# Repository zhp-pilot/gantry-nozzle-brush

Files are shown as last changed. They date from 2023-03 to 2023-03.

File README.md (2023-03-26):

# Gantry mounted nozzle brush for V2 and Trident TAP users.

Gantry Nozzle Scrubber_small

## CREDITS

This is an adaptation of the Decontaminator Nozzle Scrubber by [edwardyeeks]( https://mods.vorondesign.com/detail/eiGz71BOprk2GapXbQVgA). The mount is derived from the fixed Klicky mount by [jlas1]( https://github.com/jlas1/Klicky-Probe).

## DISCLAIMER 

***THIS MOD IS INTENDED FOR ADVANCED USERS ONLY AND WILL REQUIRE SETTING UP YOUR PRINTER WITH VERY TIGHT TOLERANCES, LIKELY REQUIRING MODIFYING YOUR Y-MAX AND ADJUSTING YOUR PHYSICAL BED LOCATION IF YOU WANT TO RETAIN THE FULL XY BUILD AREA OF YOUR PRINTER. READ THIS WRITE UP AND THE PROVIDED CONFIG FILE IN THEIR ENTIRITY BEFORE PROCEEDING. YOU ARE USING THIS MOD AT YOU OWN RISK AND THE AUTHOR ASSUMES NO LIABILTY FOR ANY DAMAGE RESULTING FROM ITS USE.***

## PURPOSE
This mod is intended for users of TAP to provide a safe nozzle cleaning routine that can be performed at the end of the print. With the original Nozzle Scrubber mod, the Z has to lower to the brush, risking crashing the toolhead into printed parts if performed at the end of a print. With this mod, the scrubbing can be performed at any height as the brush is mounted to the gantry. There are no Z movements in the provided config, as such, the cleaning will be performed at the current height when the macro is called.

**This mod is NOT recommended for Klicky, Euclid, or any variant that has a probe dock mounted on the rear gantry extrusion.** The intent is for this mount to be installed where the probe mount would typically be installed on the far left. Trying to use this mod in conjunction with another gantry-mounted mod, one risks the movements of the two interfering with each other and potentially causing damage. There are NO safety parameters in the macro to check if the movements are safe and won't collide with other objects.

## IMPORTANT INFO
On a 2.4, the gantry mount needs to be installed so that it clears the bed extrusions. On a standard bed install, the mount will hit the extrusion during homing, QGL, and bed mesh operations, and maybe even when the nozzle is at 1-2 mm or below. Remember with TAP, the gantry actually keeps moving down after the nozzle hits the bed.  I don’t have a Trident to test on, but I assume the same would hold true for the rear bed mount extrusion.

The standard gantry mount has an overall height of 80mm and a depth of 72mm (excluding the brush holder). The mount is height adjustable by 3mm via slotted holes. If you find these dimensions do not work for you, the Fusion360 file is parametric. There are two User Parameters, one for height and one for depth, that you can change to easily update the model. If you are unfamiliar with parameters in Fusion360, click on the Modify drop down and select Change Parameters at the bottom. To change the dimension, click on the value in the Expression column.

It's a tight fit installing this and will require some testing/adjustments on your behalf. My current setup is probably the worst-case scenario at this point for the amount of space needed for Stealthburner/CW2 or other CW2-mount extruder mods. With TAP you lose ~3mm of real estate over the standard X-carriage. I also have the Enclosed Orbiter 2.0 mod, and with this, the Stealthburner cowling is pushed out another 1mm or so. Additionally, I'm using hartk's mod to relocate the Y-endstop to the A-motor mount which limits how far back the X-gantry will go. On my 350 build, I have my Y-max set at 355. The back of the bed is at 350, which is approximately 2mm off the brush measured from the nylon body of the brush as it sticks out slightly. I have 3mm foam on my doors and with the toolhead at X0, there's about 2mm of space between the cowling and door. This limits the hotend fan's performance so be aware of that and don't leave your toolhead parked at X0 and heated for an extended amount of time. The only time mine is there is for a few seconds for the purge line. Also, the type and location of your Y-endstop can also affect your useable space. I removed the lever on the switch which allowed the X-carriage to go back another 1mm or so. **Play around with the setup and see what works. Make sure you manually move the toolhead around and check for clearances. If you feel it won’t fit and you still want to use this mod, then you may need to limit your printable Y dimension (e.g. set your Y-max at 350 and update you slicer bed profile to have a Y-dimension of 345). YMMV.**

Since the mount will be so close to the bed, having rear stops for your build plate is highly recommended. I’ve included an STL of a slightly modified version from the original Purge Bucket and Nozzle Scrubber mod. This uses M3 SHCS instead of the M2 self-tappers in the original. Use M3x8 SHCS and place the stops on the bed mount extrusions in direct contact with your bed. Please pay attention to these over time. Since they in direct contact with bed they can be prone to warping and the screws start leaning back. Also, if you aren’t careful putting the build sheet on you can break these. **Be very careful and check these regularly. Print some extras at the beginning to have some backups.**

## PARTS REQUIRED
- Brass or nylon brush ([Amazon](https://www.amazon.com/gp/product/B08P4DSTCM/ref=ppx_yo_dt_b_search_asin_title?ie=UTF8&psc=1) or [AliExpress](https://www.aliexpress.com/item/33053117369.html?spm=2114.12010615.8148356.2.315e106dfzI86U))
- 2x M3 brass threaded inserts (Voron spec)
- 2x M3x12 or M3x16 SHCS
- 2x M5x10 BHCS and 2x M5 T-nuts
- 4x M3x8 SHCS and 2x M3 T-nuts (for rear bed stops)

## ASSEMBLY
### GANTRY NOZZLE BRUSH
- Install M3 brass threaded inserts into the gantry mount.
- Install the brush holder on the gantry mount with either M3x12 SHCS or M3X16 SHCS.
- Install modified brush into the brush holder. See edwardyeeks mod [here]( https://mods.vorondesign.com/detail/eiGz71BOprk2GapXbQVgA) for more information if you aren’t familiar with this.
- Install mount to the rear gantry extrusion using M5x10 BHCS.
- Setup config file following the directions in the file.

### BED STOPS
- Install M3x8 SHCS into top holes a few mm. These are installing into plastic so be careful.
- Install the stops to the bed mount extrusions using M3x8 SHCS. Make sure they are in contact with the bed.
- Adjust the top M3 screws as needed so they are just proud of your bed/magnet. Just high enough you can reference your build sheet on while installing.
- Carefully look at the installed build sheet and confirm it's flush with the back of the bed. Any overhang reduces the clearance you have for the brush. 

## ADDITIONAL INFO
I use this mod as part of the print_end macro. It's important to have an adequate retract to limit oozing after the nozzle is cleaned. I turn the heaters off early and added a 15 sec wait command before calling the clean_nozzle macro. This allows any oozing that's going to happen to occur before the clean. You'll have to experiment with this to find what works best for you.

Example:
```
[gcode_macro PRINT_END]
gcode:    
    # safe anti-stringing move coords
    {% set th = printer.toolhead %}
    {% set x_safe = th.position.x + 20 * (1 if th.axis_maximum.x - th.position.x > 20 else -1) %}
    {% set y_safe = th.position.y + 20 * (1 if th.axis_maximum.y - th.position.y > 20 else -1) %}
    {% set z_safe = [th.position.z + 2, th.axis_maximum.z]|min %}
    SAVE_GCODE_STATE NAME=STATE_PRINT_END
    M400                    ; wait for buffer to clear
    TURN_OFF_HEATERS        ; turn off bed and extruder heaters
    G92 E0                  ; zero the extruder
    G1 E-2.0 F2000          ; retract filament
    G90                     ; absolute positioning
    G0 X{x_safe} Y{y_safe} Z{z_safe} F10000  ; move nozzle to remove stringing
    G1 E-10.0 F5000         ; retract filament more
    G0 X{th.axis_maximum.x//2} Y{th.axis_maximum.y - 2} F3600  ; park nozzle at rear
    G4 P15000               ; wait 15 secs for nozzle to start cooling
    STATUS_CLEANING         ; set LEDs to cleaning
    CLEAN_NOZZLE            ; clean nozzle on brush
    M107                    ; turn off part cooling fan
    BED_MESH_CLEAR          ; clear bed mesh
    STATUS_READY            ; set LEDs to ready
    RESTORE_GCODE_STATE NAME=STATE_PRINT_END
 ```

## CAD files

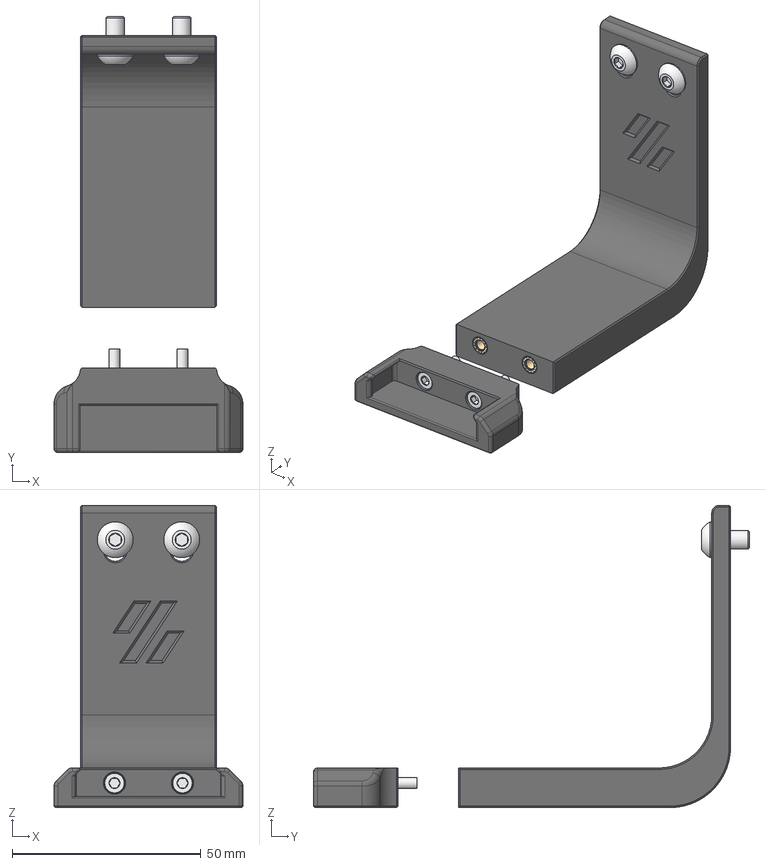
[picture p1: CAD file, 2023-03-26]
CAD/Gantry_Nozzle_Brush.step
50.0 x 115.4 x 80.0 mm
brush_holder
gantry_mount
M3_threaded_insert x 2
M3x12_SHCS x 2
M5x10_BHCS x 2

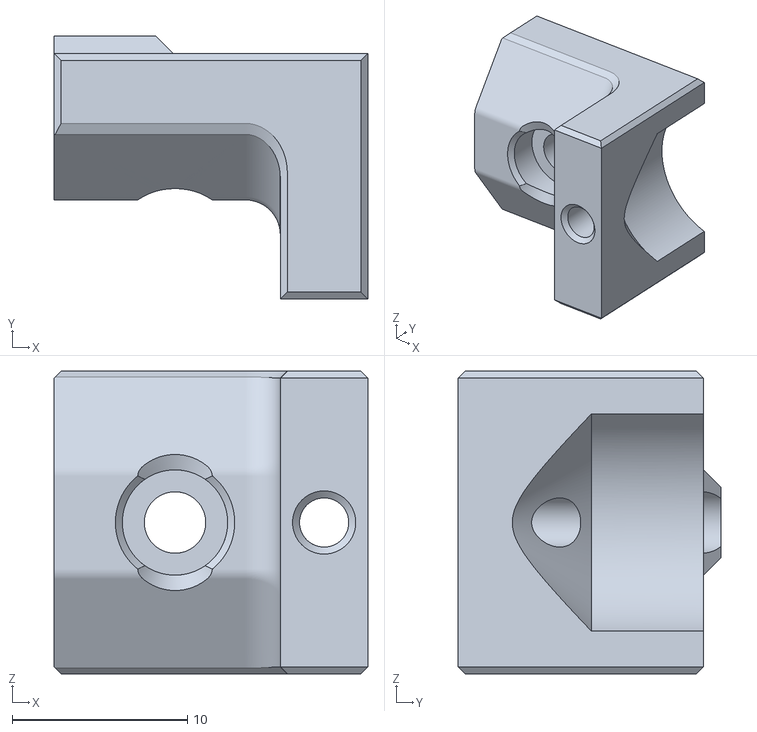
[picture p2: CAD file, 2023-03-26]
STLs/sheet_stop_x2.stl
17.9 x 15.0 x 17.3

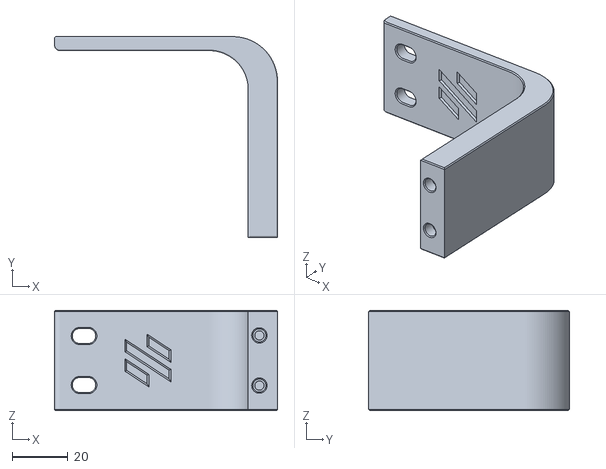
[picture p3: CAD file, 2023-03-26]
STLs/gantry_mount.stl
80.0 x 72.0 x 36.0

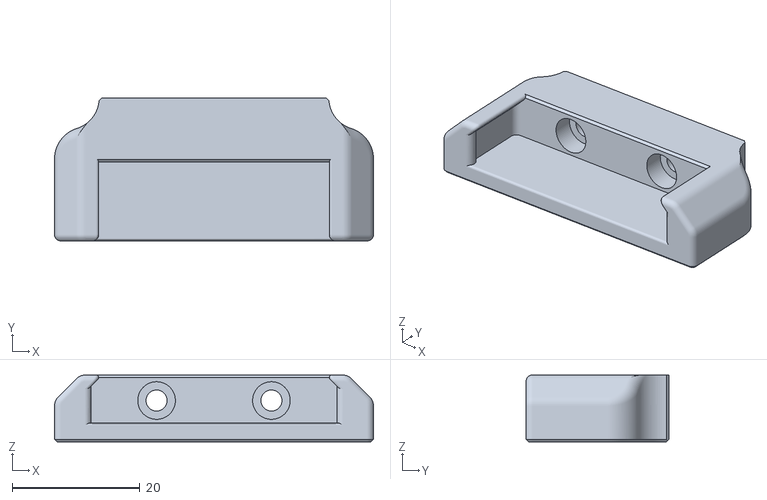
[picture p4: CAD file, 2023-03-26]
STLs/brush_holder.stl
50.0 x 22.4 x 10.5

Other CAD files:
CAD/Gantry_Nozzle_Brush.f3d

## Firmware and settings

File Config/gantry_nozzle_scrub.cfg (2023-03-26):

#######################################################################################################################################

# This macro config is to be used in conjunction with the Ganrty Nozzle Scrubber mod by zhp_pilot (zhp_pilot#9778 on Discord). Based on
# the original Purge Bucket & Nozzle Scrubber mod by Hernsl (hernsl#8860 on Discord) and edited by Edwardyeeks (edwardyeeks#6042 on
# Discord).

# This mod and macro is intended for users of TAP to provide a safe nozzle cleaning routine that can be performed at the end of print.
# With the original Nozzle Scrubber mod, the z has to lower to the brush, risking crashing the toolhead into printed parts if performed
# at the end of a print. With this mod, the scrubbing can be performed at any height as the brush is mounted to the gantry.
# There are no z movements is this macro, as such, the cleaning will be performed at the current height when the macro is called.

# This mod and macro are NOT recommended for Klicky, Euclid, or any variant that has a probe dock mounted on the rear gantry extrusion.
# The intent is for this mount to be installed where the probe mount would typically be installed on the far left. Trying to use this
# mod in conjunction with another gantry mounted mod, one risks the movements of the two interfering with each other and potentially
# causing damage. There are NO safety parameters is the macro to check if the movements are safe and won't collide with other objects.
# IF THE USER DECIDES TO DO THIS ANYWAY, THEY ARE DOING SO AT THERE OWN RISK.

# This config assumes the brush is installed on the left side of the rear gantry extrusion. The variables allow for other positions but
# note the start position for the wiping is on the right side of the brush. The wiping finishes on the right side of the brush then the
# toolhead returns to the rear center position just like the default print_end macro. 

# Default parameters are set for safe speeds. The default location is based on the mount being installed on the left side
# of the rear gantry extrusion in contact with the B-motor mount. Where necessary, tweak the parameters to fit your printer.

# Upload this config file (gantry_nozzle_scrub.cfg) into the same directory as printer.cfg. Once uploaded, add the following to your
# printer.cfg: [include ganrty_nozzle_scrub.cfg]

#######################################################################################################################################

# Name of the macro is clean_nozzle.

[gcode_macro clean_nozzle]

# These parameters define your travel and scrubbing speeds, and how many times you want to wipe. Update as necessary.

variable_prep_spd_xy:        4000	         ; Travel (not cleaning) speed along x and y-axis in mm/min.
variable_wipe_spd_xy:        6000	         ; Nozzle wipe speed in mm/min.
variable_wipe_qty:              6	         ; Number of complete wipes (A complete wipe is full left and right motion).

# These parameters define the size of the brush. A visual reference is provided below. Update for your install. A negative is included
# to throw a Move Out of Range error if you don't set this up. The default values provided should be adequate for a left install
# against the B-motor mount; however, you still need to confirm this.
# 
#          ←offset→←   brush_width   →←offset→
#                   _________________                                                          
#                  |                 |
#  brush_start (x) |                 |
#                  |_________________|     
#                          (y)
#                      brush_front
# __________________________________________________________
#                     PRINTER FRONT 

variable_brush_start:     -28
variable_brush_width:     -34

# Offset is used to make the nozzle clear the brush on each side during the wipe. I found this generally provides a better clean.
# Recommended valve is 6. If you want the nozzle to stay within the brush during the wipe set this to 0.

variable_brush_offset:     6	

#######################################################################################################################################
#######################################################################################################################################

### From here on, unless you know what you're doing, it's recommended to not change anything.

#######################################################################################################################################
#######################################################################################################################################

gcode:
     
   # First, check if the axes are homed.
   {% if "xyz" in printer.toolhead.homed_axes %}

      ## Save the gcode state in this macro instance.
      SAVE_GCODE_STATE NAME=clean_nozzle

      ## Set to absolute positioning.
      G90

      ## Define toolhead
      {% set th = printer.toolhead %}

      ## Grab max position of Y-axis from config.
      {% set Ry = printer.configfile.config["stepper_y"]["position_max"]|float %}

      ## Position for wipe.
      G1 X{brush_start + brush_width + brush_offset} Y{Ry} F{prep_spd_xy}
             
      ## Perform wipe. Wipe direction based off bucket_pos for cool random scrubby routine.
      {% for wipes in range(1, (wipe_qty + 1)) %}
         G1 X{brush_start - brush_offset} F{wipe_spd_xy}
         G1 X{brush_start + brush_width + brush_offset} F{wipe_spd_xy}
      {% endfor %}
   
      ## Clear from area, park nozzle at rear
      G0 X{th.axis_maximum.x//2} Y{th.axis_maximum.y - 2} F{prep_spd_xy}
      
      ## Restore the gcode state to how it was before the macro.
      RESTORE_GCODE_STATE NAME=clean_nozzle

   {% else %}

      ## raise error will stop any macros that clean_nozzle is referenced in from proceeding for safety.
      { action_raise_error("Please home your axes!") }
      M117 Please home first!

   {% endif %}
